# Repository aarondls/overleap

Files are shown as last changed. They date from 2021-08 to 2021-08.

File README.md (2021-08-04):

# Overleap

<p align="center">
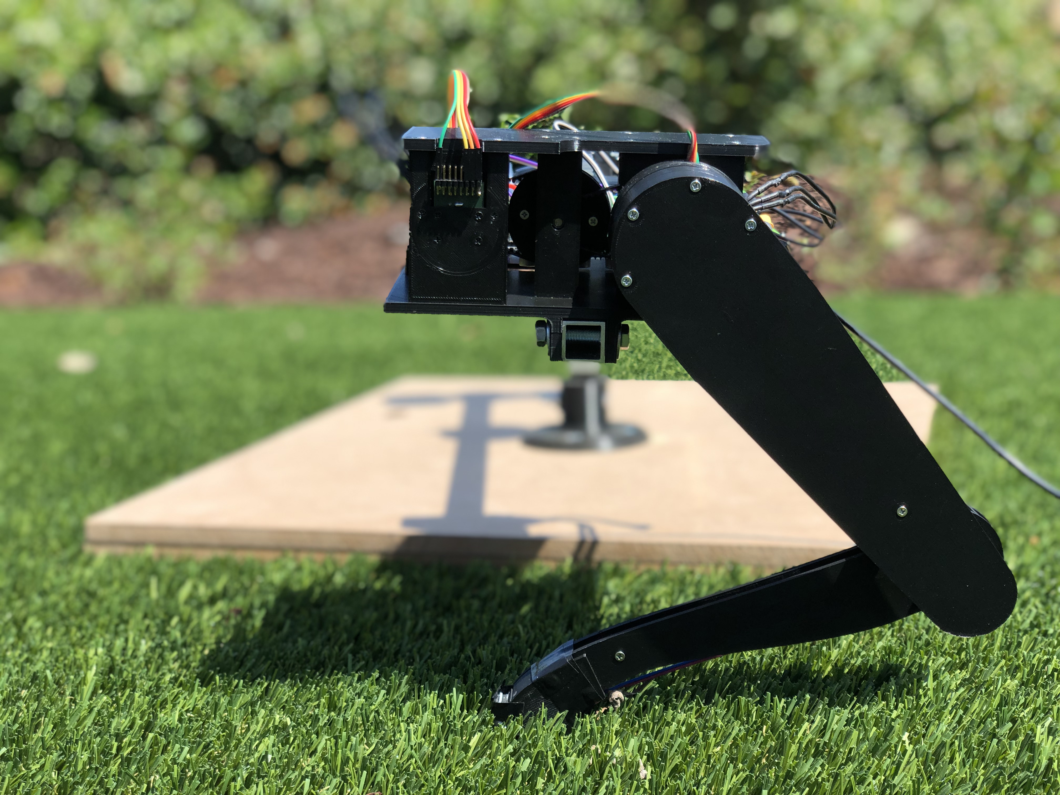
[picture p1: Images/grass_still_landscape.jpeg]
  
</p>

## Overview

Overleap is an open-source low-cost 3D printed dynamic robotic leg designed be as accessible as possible. Overleap can be assembled with a 3D printer and minimal tools, without CNC milling / waterjet cutting / laser cutting like other robotic legs. The building process is tailored to be simple and seamless, from the assembly manual to the programming method, creating a unique assembly experience.

Overleap is capable of executing quick and dynamic movements such as jumping and continuous hopping in a circle. This is made possible through Overleap's quasi-direct drive actuators and custom foot contact sensor. Jumping is controlled by directly manipulating joint torque, as calculated by the desired foot force and the Jacobian of the leg.

In the future, overleap is planned to be used in other legged projects, such as a low-cost quadruped robot.

## Capabilities

Overleap can perform a single jump

<p align="center">
  
</p>

as well as continous hopping in a circle

<p align="center">
  
</p>

The height and stance time of each jump, as well as horizontal speed of the leg, can be varied as desired.

## Design

<p align="center">
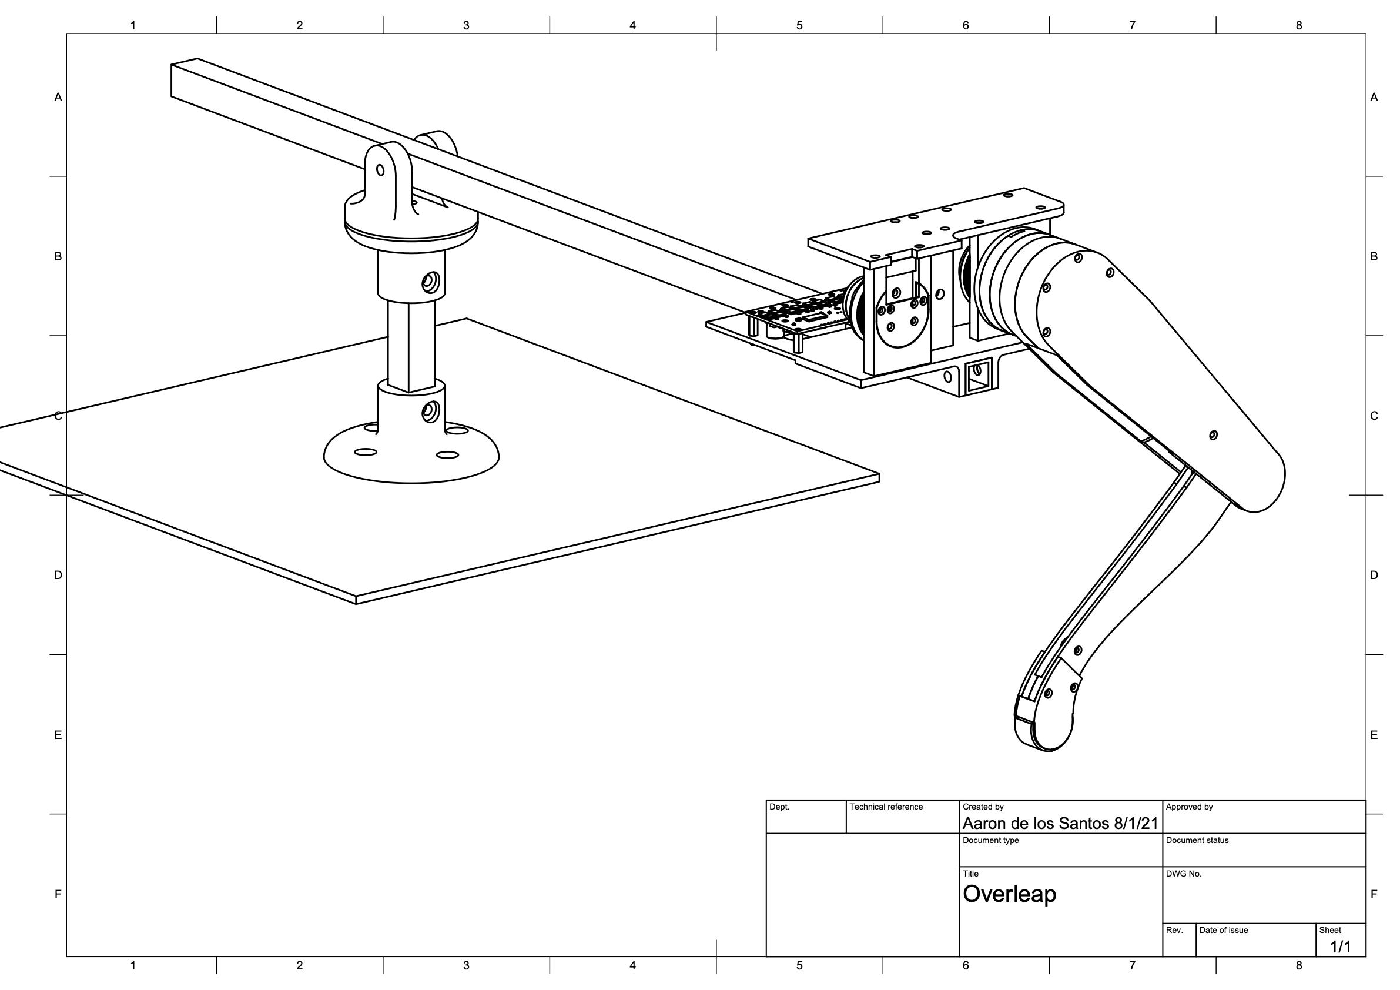
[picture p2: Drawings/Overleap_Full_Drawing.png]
  
</p>

### Quasi-Direct Drive Actuation

Overleap uses quasi-direct drive actuators to drive the leg. The motors are geared down 9:1, allowing for increased torque while having high backdrivability and bandwidth.

To keep the footprint small, the gear system for the hip joint is housed beside the hip, while the gear system for the knee joint is housed within the upper leg. The actuators are coaxial in the sense that the knee motor is on the same axis as the hip motor output shaft.

### Custom foot contact sensor

A custom foot contact sensor was developed to detect when overleap was on the ground. This foot sensor is cheap and requires no machining/moulding.

The foot sensor consists of a 3D printed frame and rubber outer padding for grip. Force detection is made possible through the use of a force sensitive resistor mounted between the outer foot pad and the frame.

The minimum actuation force of the foot sensor is around 10 grams, and can be increased in software depending on the desired conditions.

### 2 DOF rotating base

For testing overleap, the leg is attached to a rotating base with 2 degrees of freedom. This allows the leg to move in both the vertical and horizontal (circular) direction.

The base plate is made out of presswood, while the actual rotating mechanism consists of 3D printed parts. Square aluminum tubes are used as the stand and boom to attach the leg.

### Controlling leg movement

Overleap works by directly controlling the torque of both motors. The microcontroller sends ASCII commands through UART to the ODrive motor controller for the desired torque of each axis. The calculation for these values of torque depends on the current phase of the leg.

During the stance phase (when the foot is touching the ground), overleap calculates a sinusoidal force profile that provides the desired impulse to the leg, then applies this force profile throughout the duration of the stance phase. To calculate the necessary torque values that achieve the desired force at the foot, the transpose of the Jacobian is used.

During the aerial phase, overleap runs a PD control loop to hold a predefined position until the foot comes into contact with the ground. While inverse kinematics can be used to calculate the angles of the leg to achieve the desired foot position, overleap defines the foot position using the joint angles directly as it is easy to visualize where the foot would be.

### Force profile

The force profile in the vertical (y) direction is a sinusoidal curve, specifically of the form a sin^2(b pi t).  The parameters a and b are calculated based on the desired force impulse and stance duration, and t is the time (duration) of the force application. This allows for the regulation of jumping height as well as gradual application of force.

In the horizontal (x) direction, the force applied is a set proportion of the vertical force. Horizontal speed can then be modulated by defining the maximum horizontal force to be applied. On top of allowing for gradual force application, this also keeps the foot firmly in contact with the ground even on slippery surfaces by taking into consideration its coefficient of friction.

## Parts

The full parts list and STL models for the 3D printed parts are available at the [parts](Parts) folder.

## Assembly

### Mechanical assembly

Start by installing all the heat set inserts into the parts. After installing, they should sit flush against the plastic and feel secure when tightening screws into them.

Next, glue the magnets that came with the AS5047P encoder evaluation board onto the back of the motor. Super glue or epoxy can be used for this.

Line up the rubber pad against the inner sensing area of the force sensitive resistor and cut the rubber to the same size. This will be used as the foot pad later on.

At this point, we will need to jump ahead to one portion of the electrical assembly and solder the jumper wires to the encoder. Solder 5 cables to the A, B, I, 5V, and GND outputs of the encoder board. Take note which wire colors correspond to which outputs, as this will be needed later on.

Now, we can continue with the mechanical assembly. As they say, a picture is worth a thousand words, so this guide will be presented as a series of clean and simple drawings similar to Ikea manuals.

These illustrations are designed to be simplistic and intuitive such that the placement of screws, timing belts, and bearings can easily be inferred from them.

You can also view the [complete assembly guide](Drawings/Complete_Assembly.pdf) compiled as a single PDF.

<p align="center">
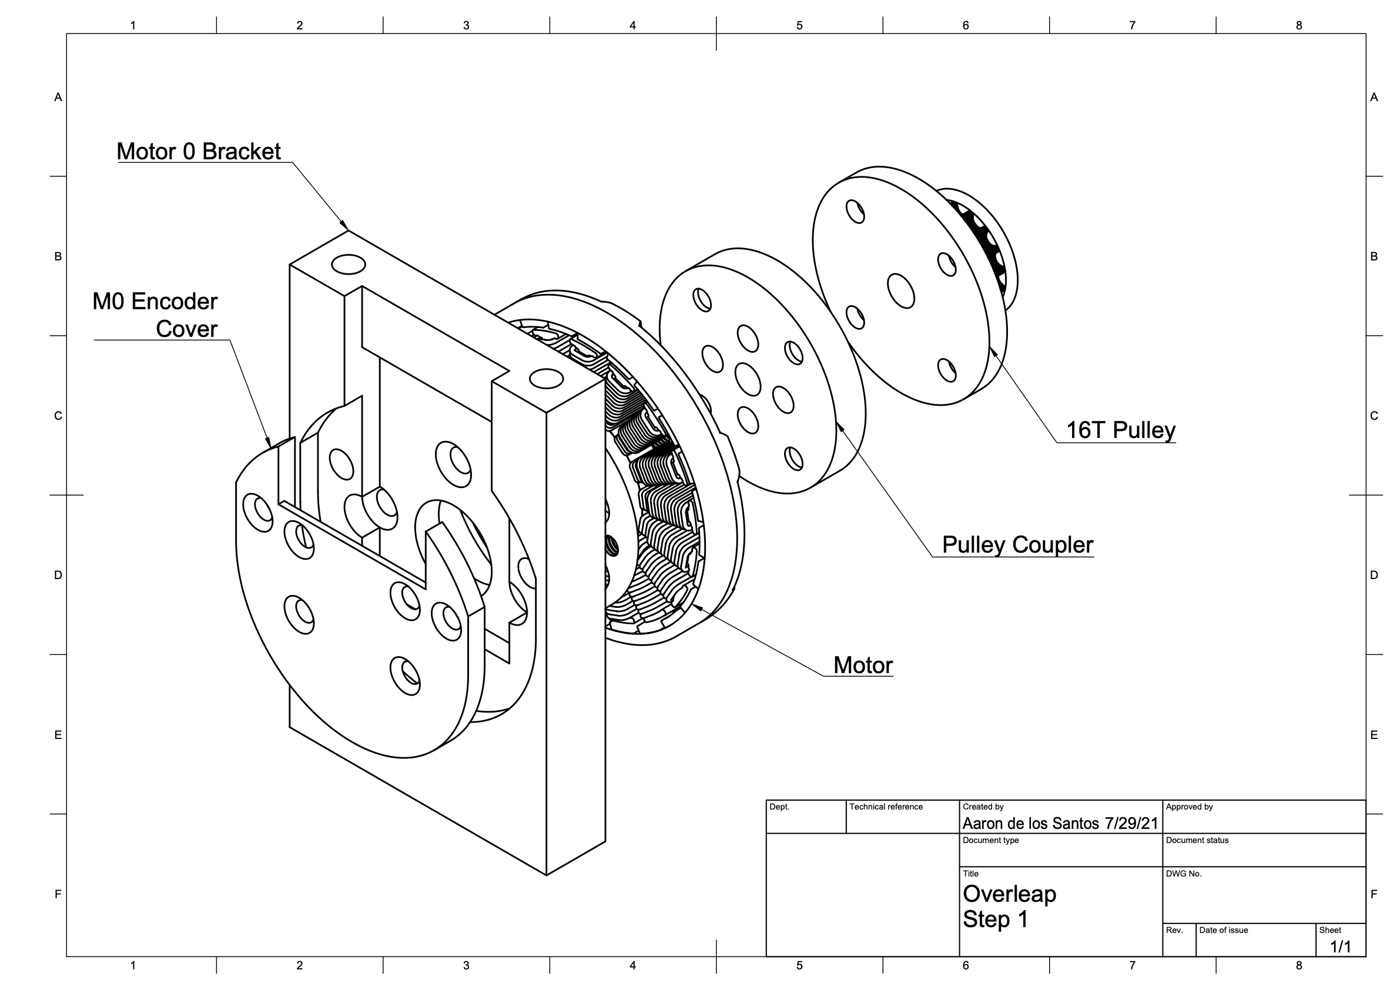
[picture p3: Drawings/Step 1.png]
  
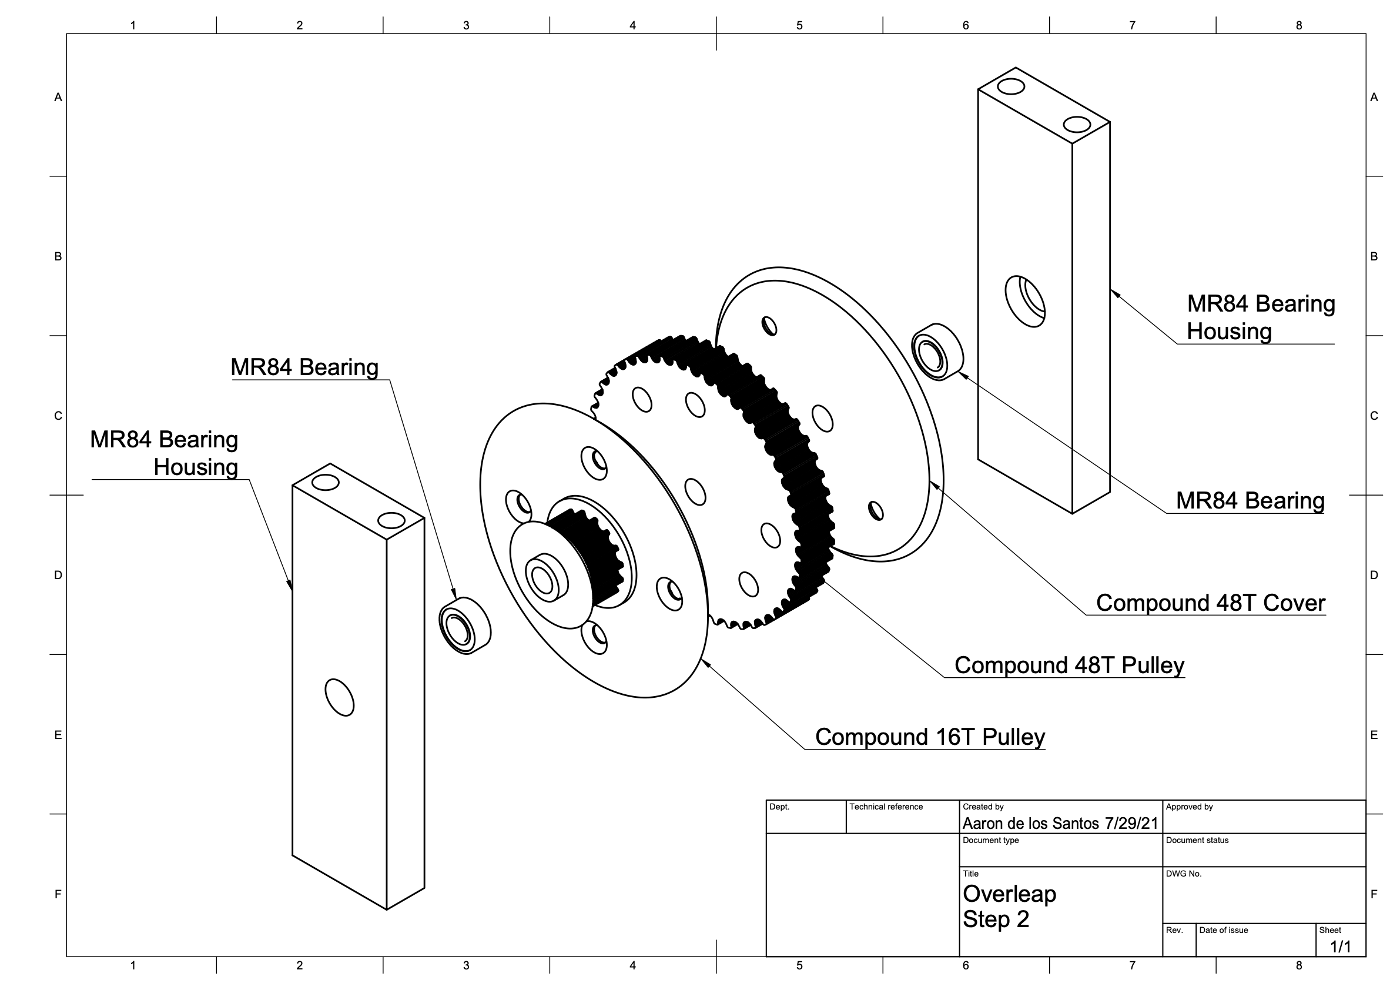
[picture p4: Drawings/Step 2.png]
  
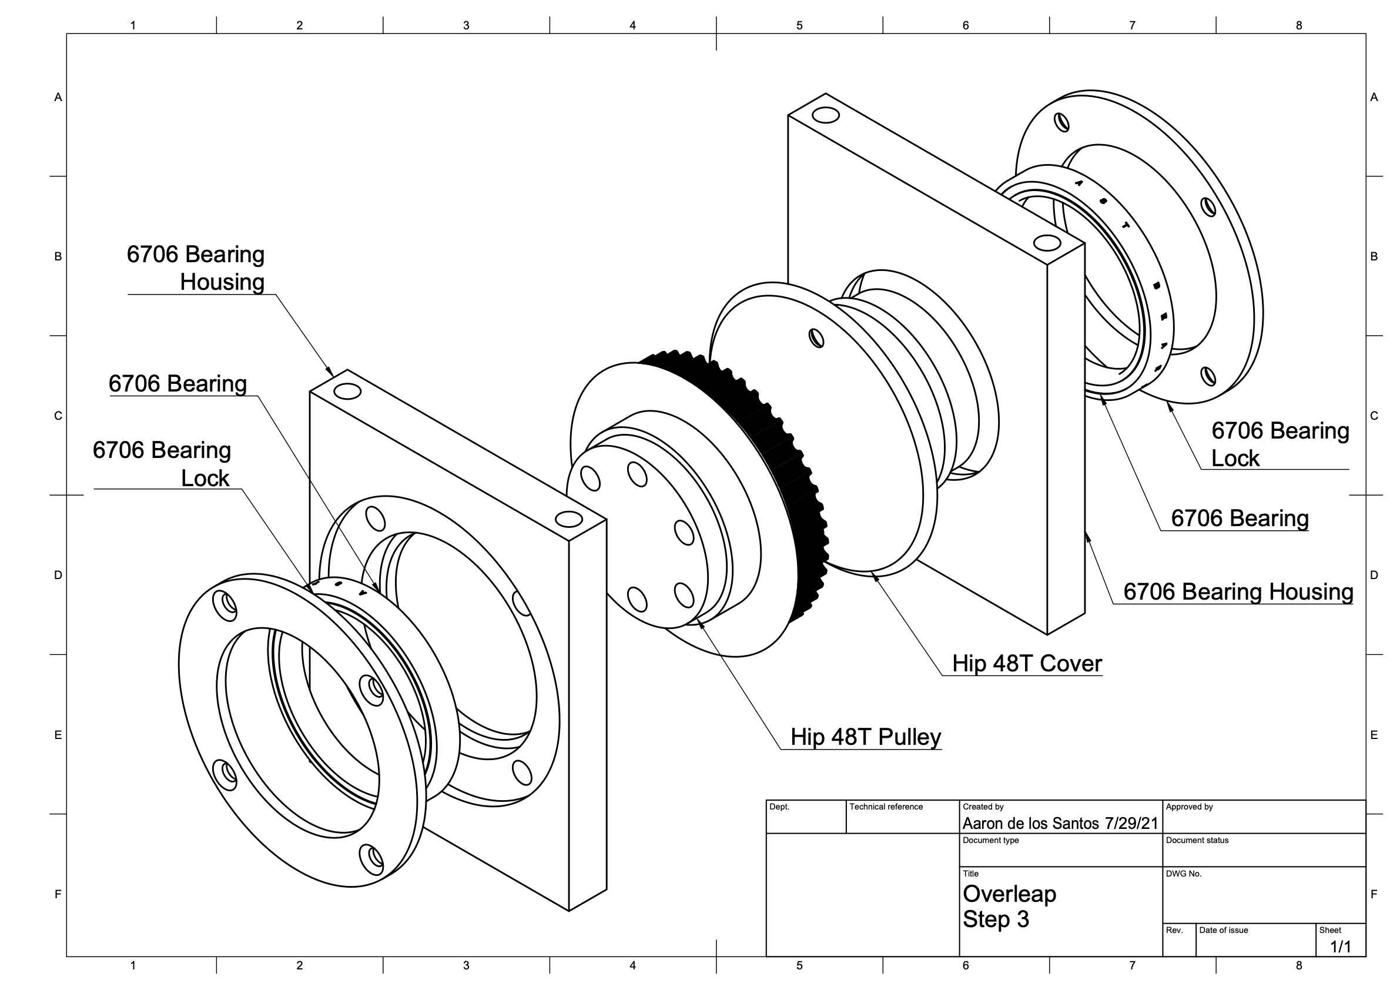
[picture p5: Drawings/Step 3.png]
  
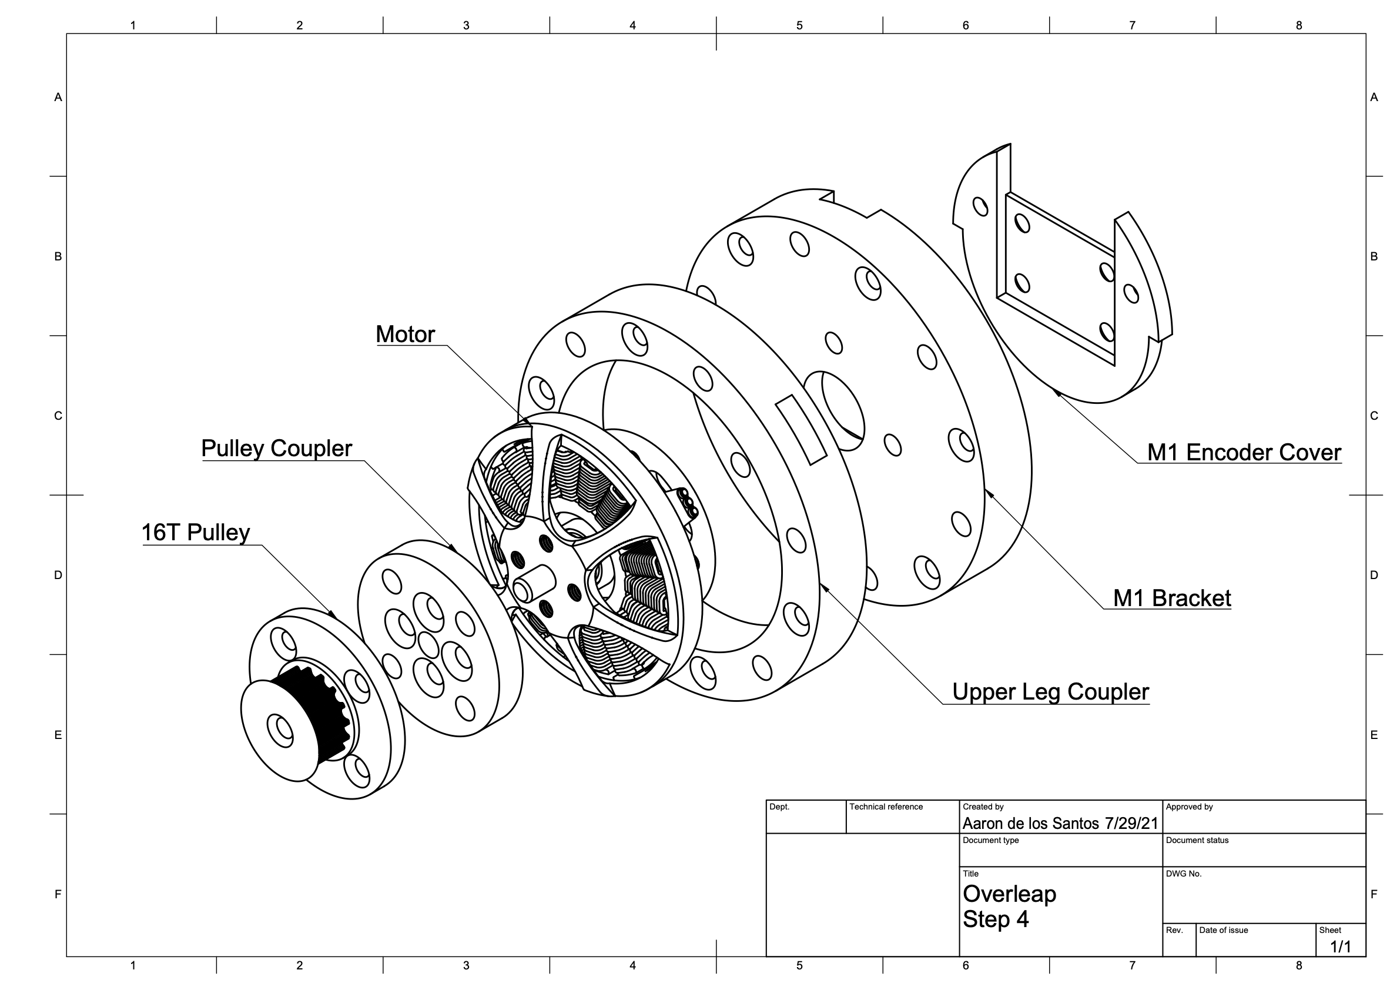
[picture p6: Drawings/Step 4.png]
  
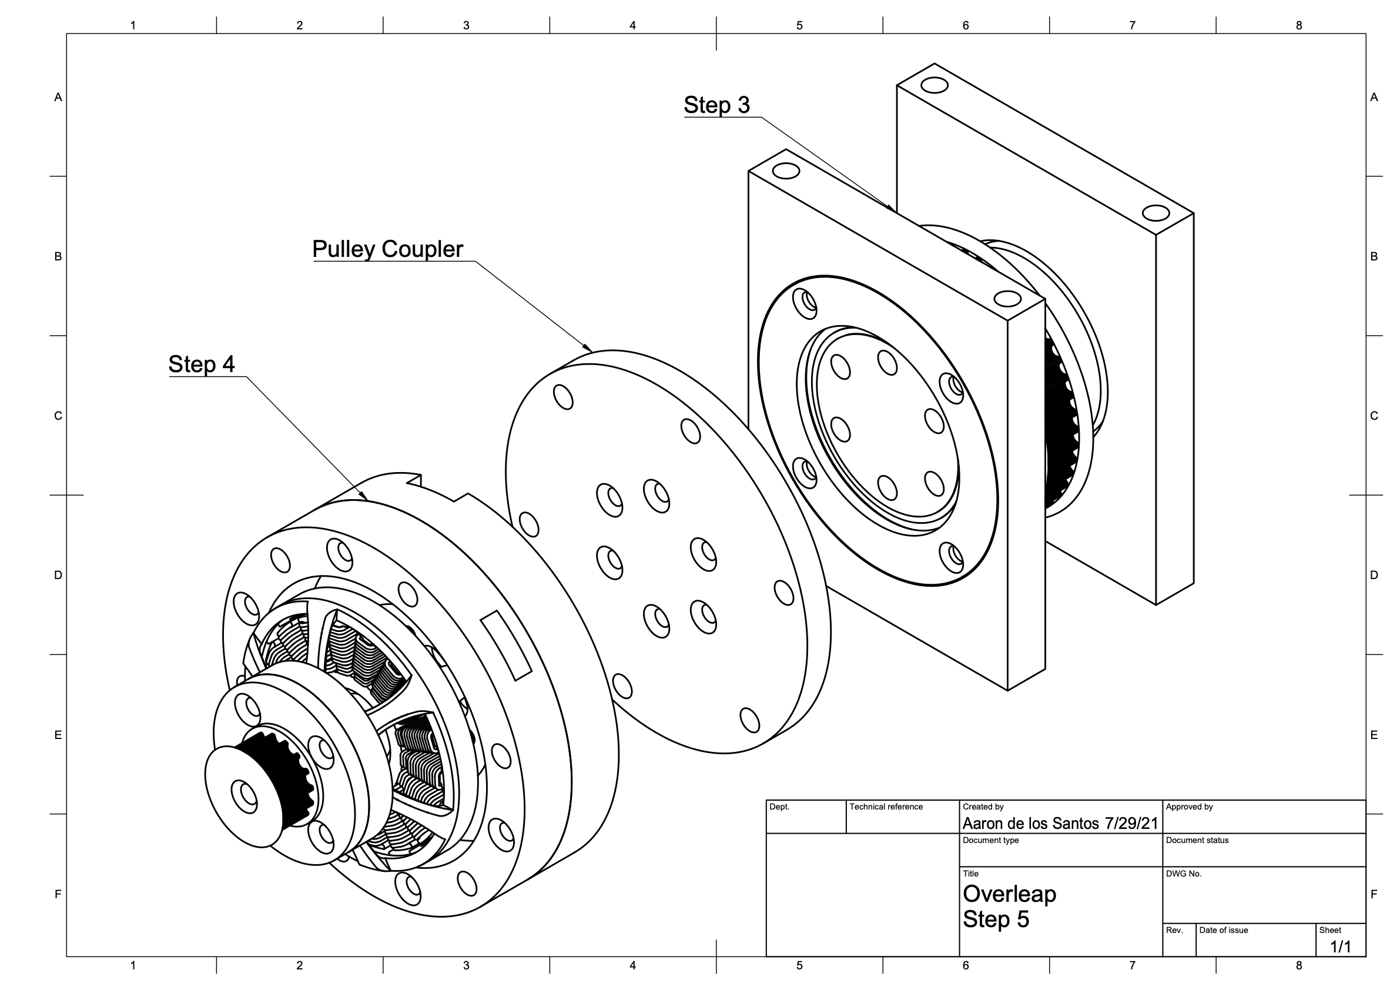
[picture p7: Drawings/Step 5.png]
  
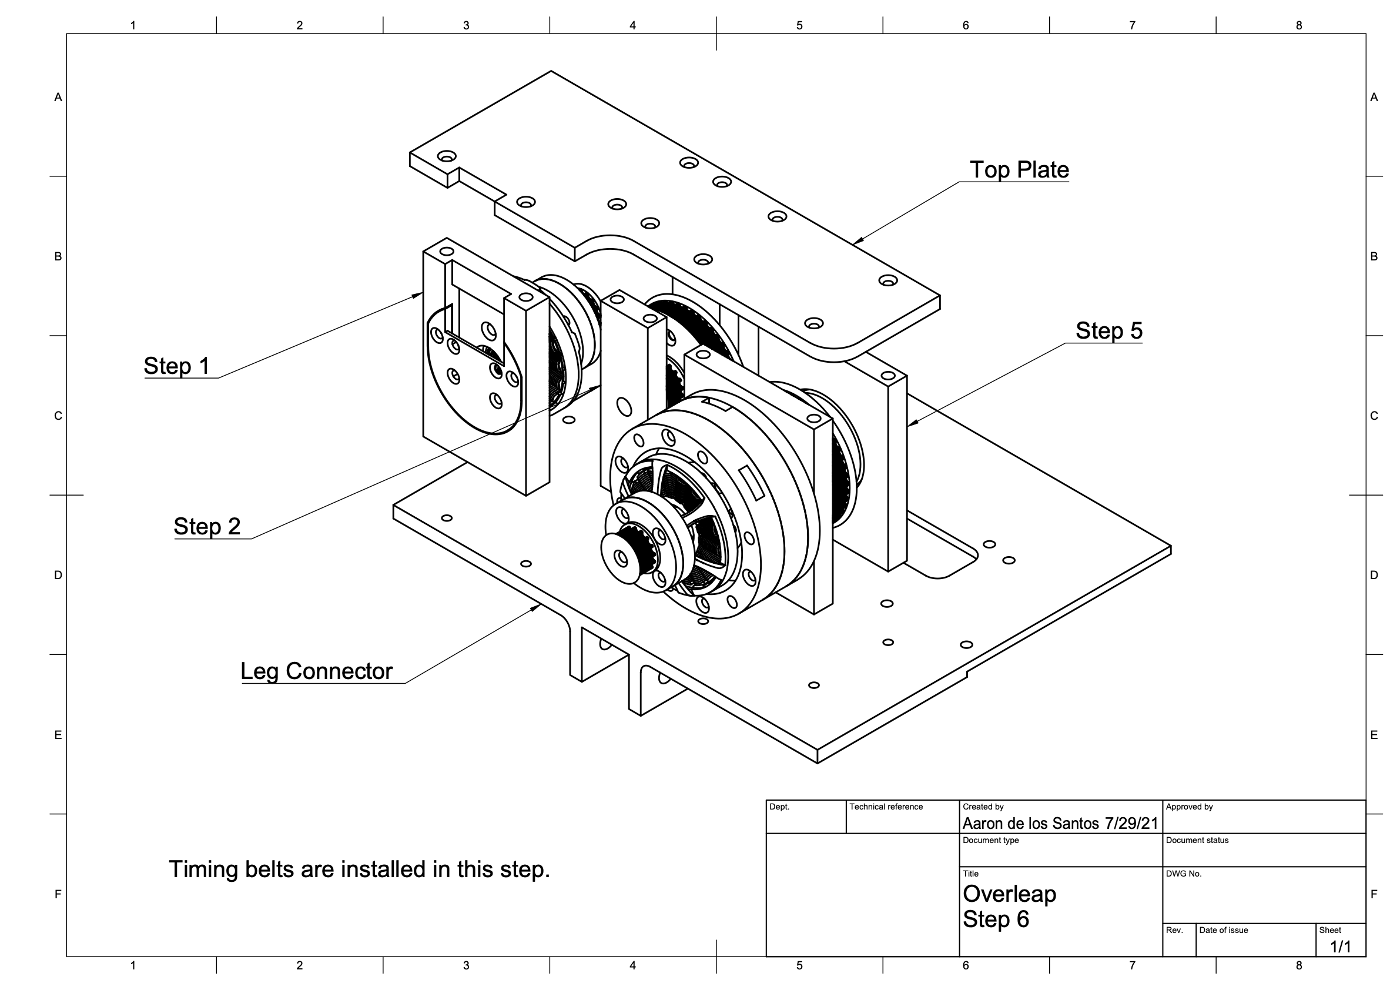
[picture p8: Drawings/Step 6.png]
  
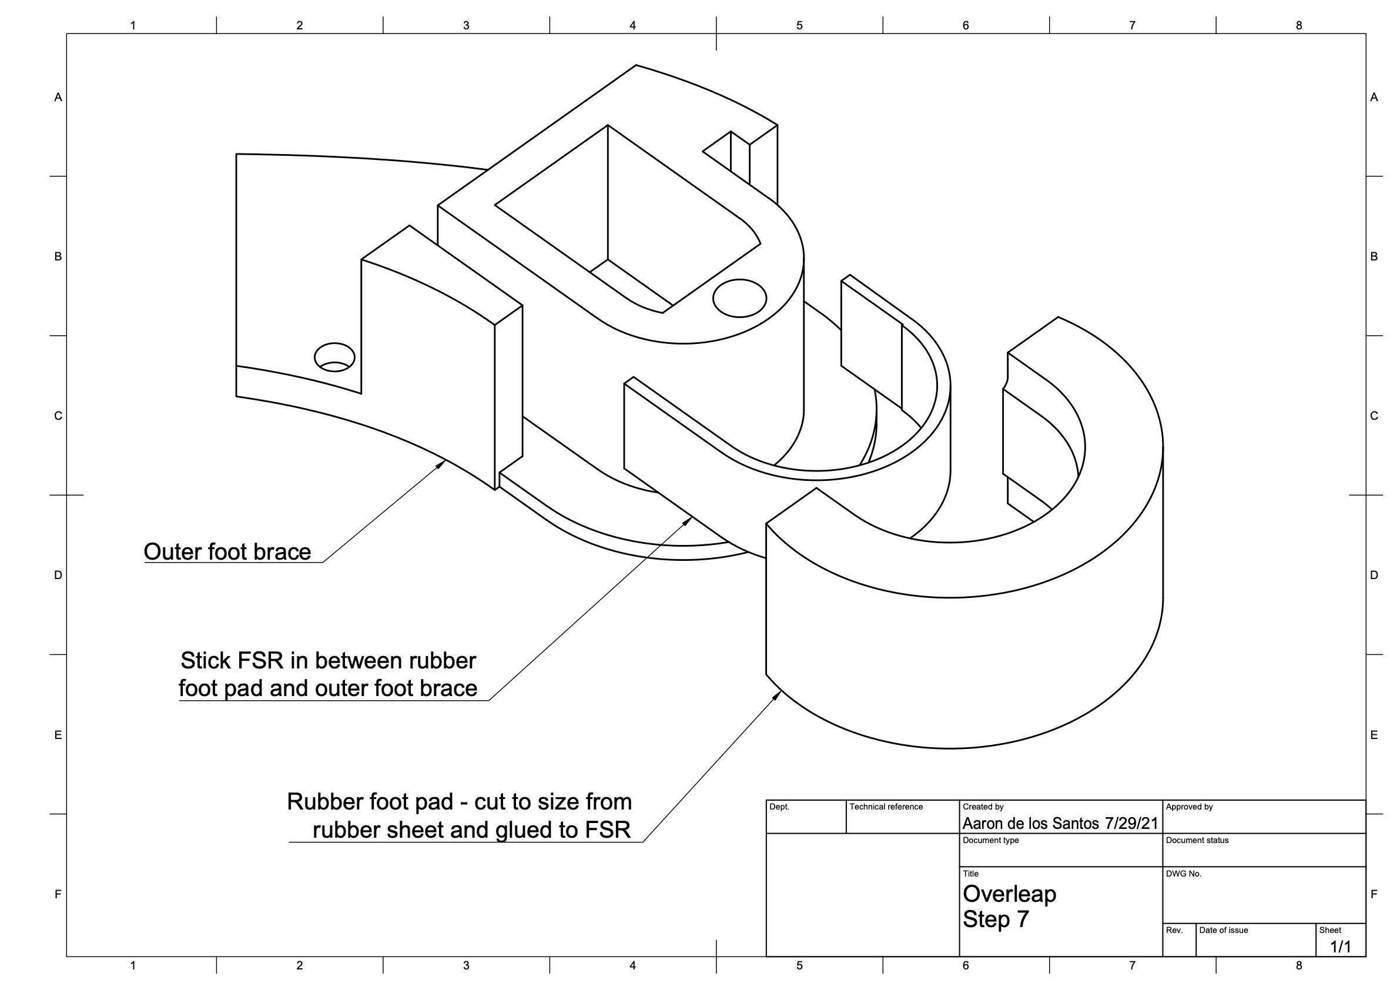
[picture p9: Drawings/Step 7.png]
  
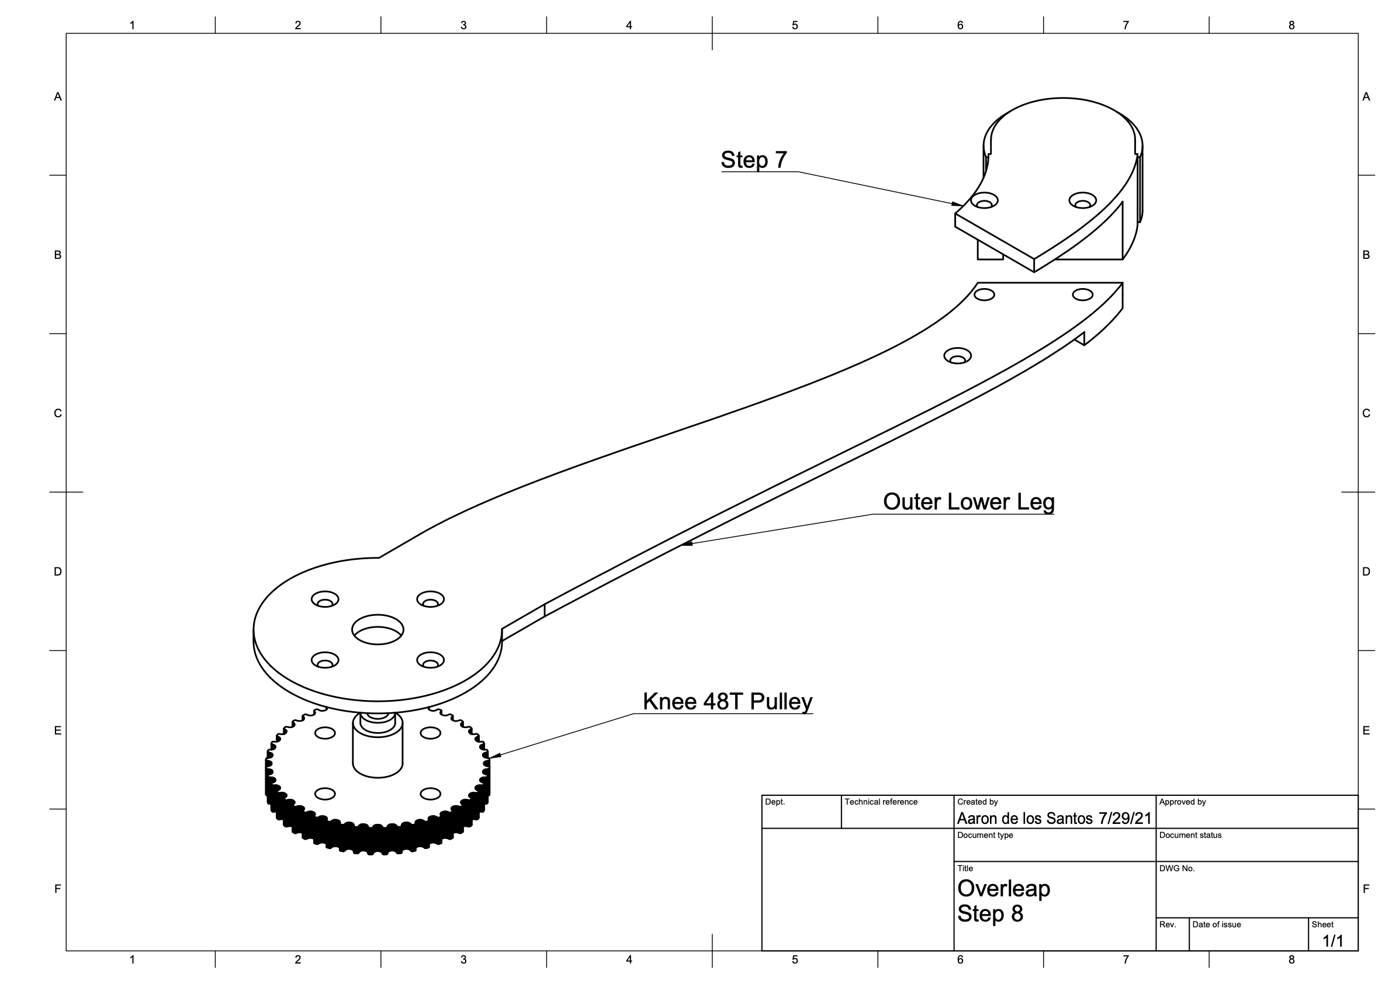
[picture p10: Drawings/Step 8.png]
  
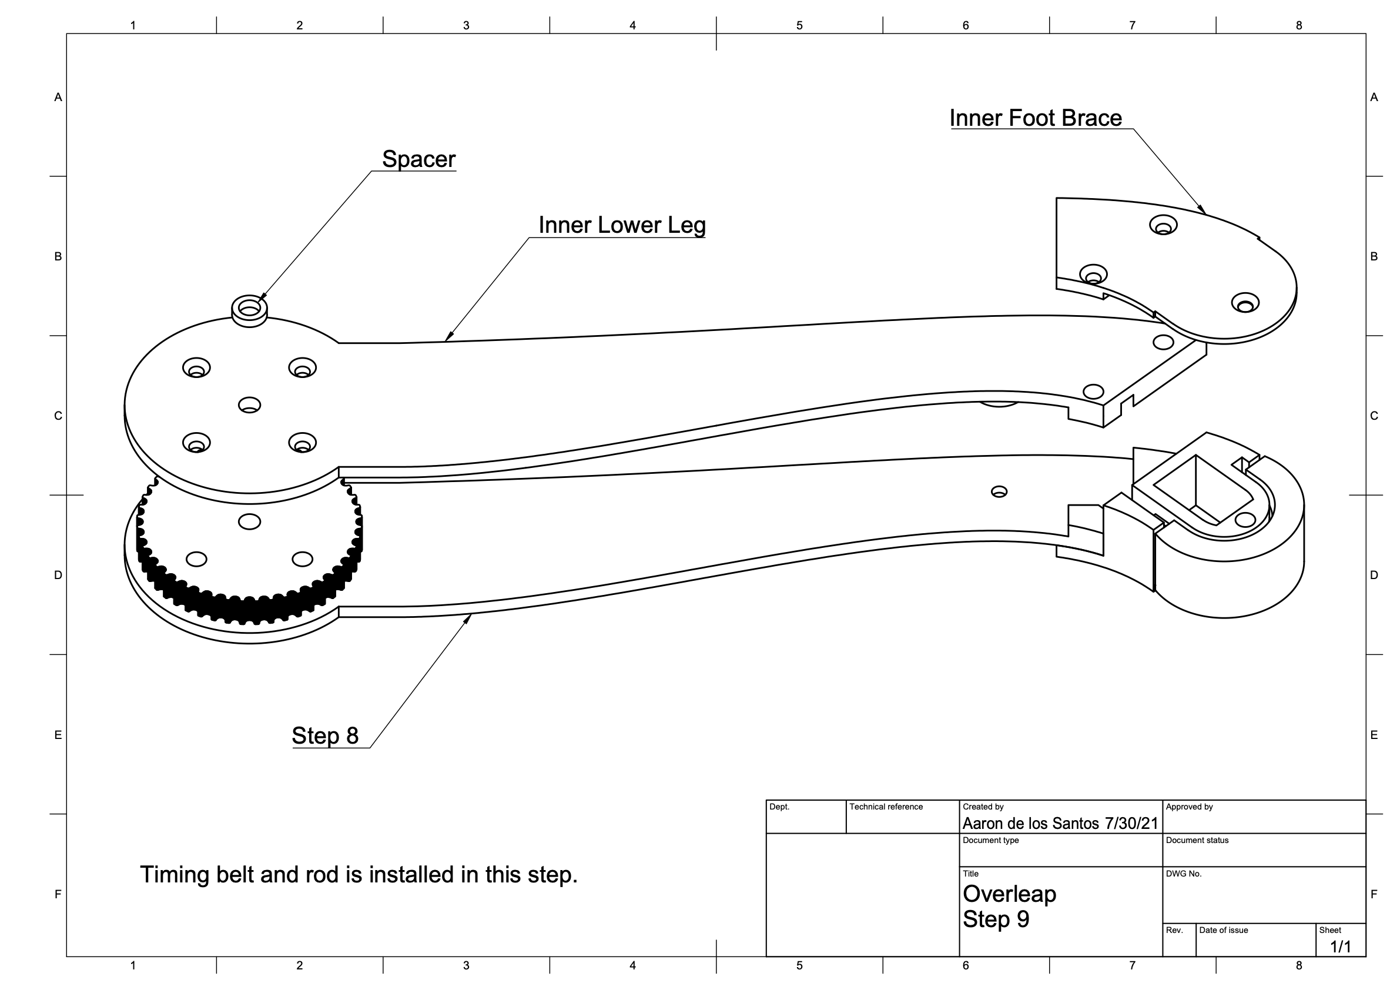
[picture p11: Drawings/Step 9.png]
  
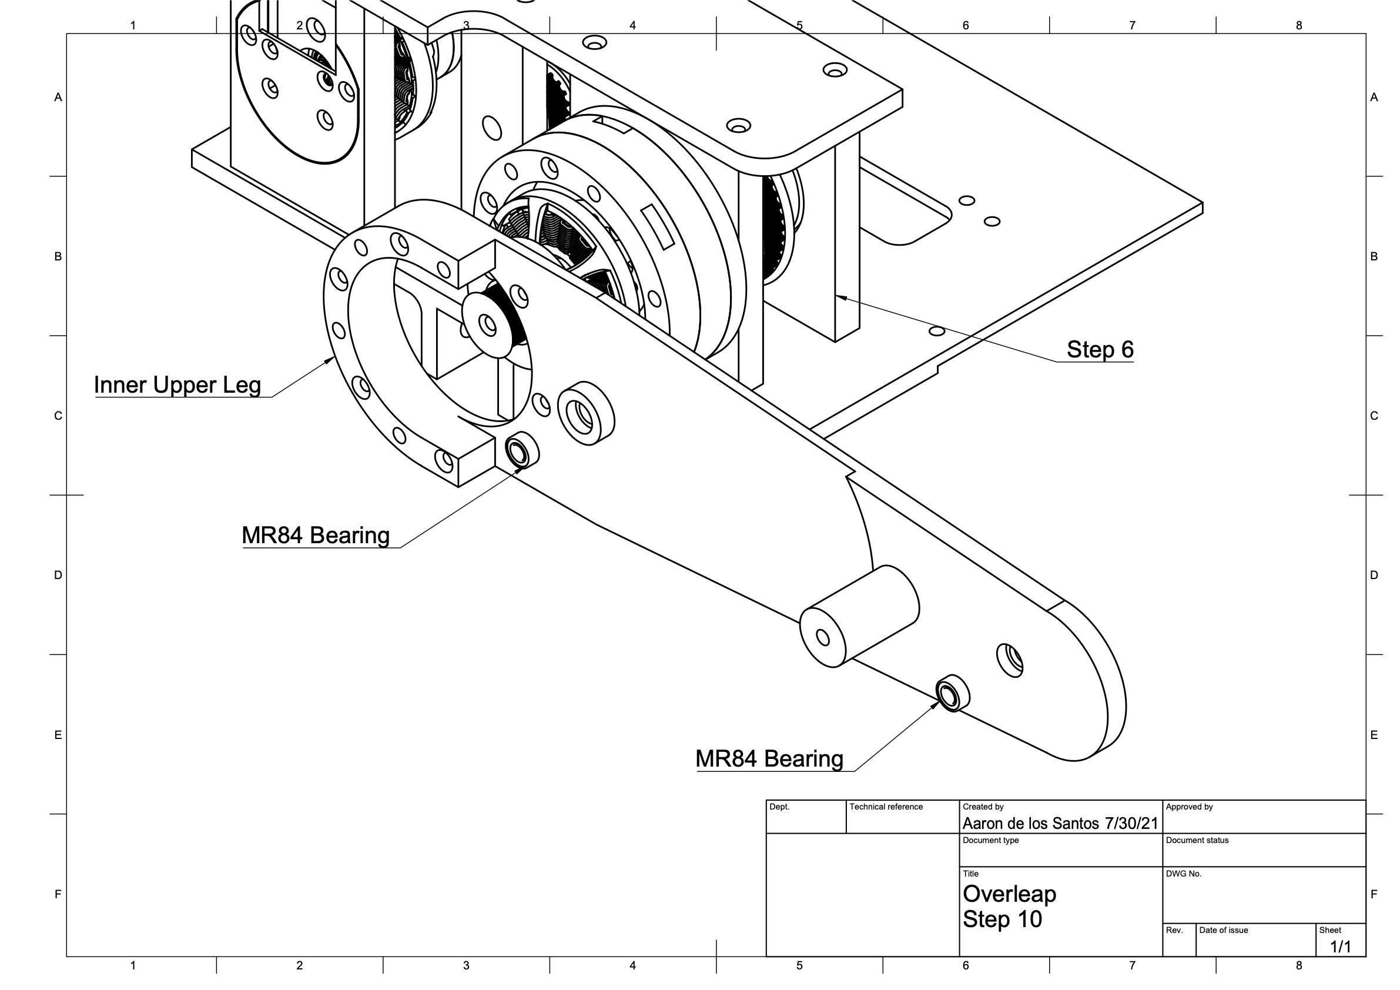
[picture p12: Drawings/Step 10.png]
  
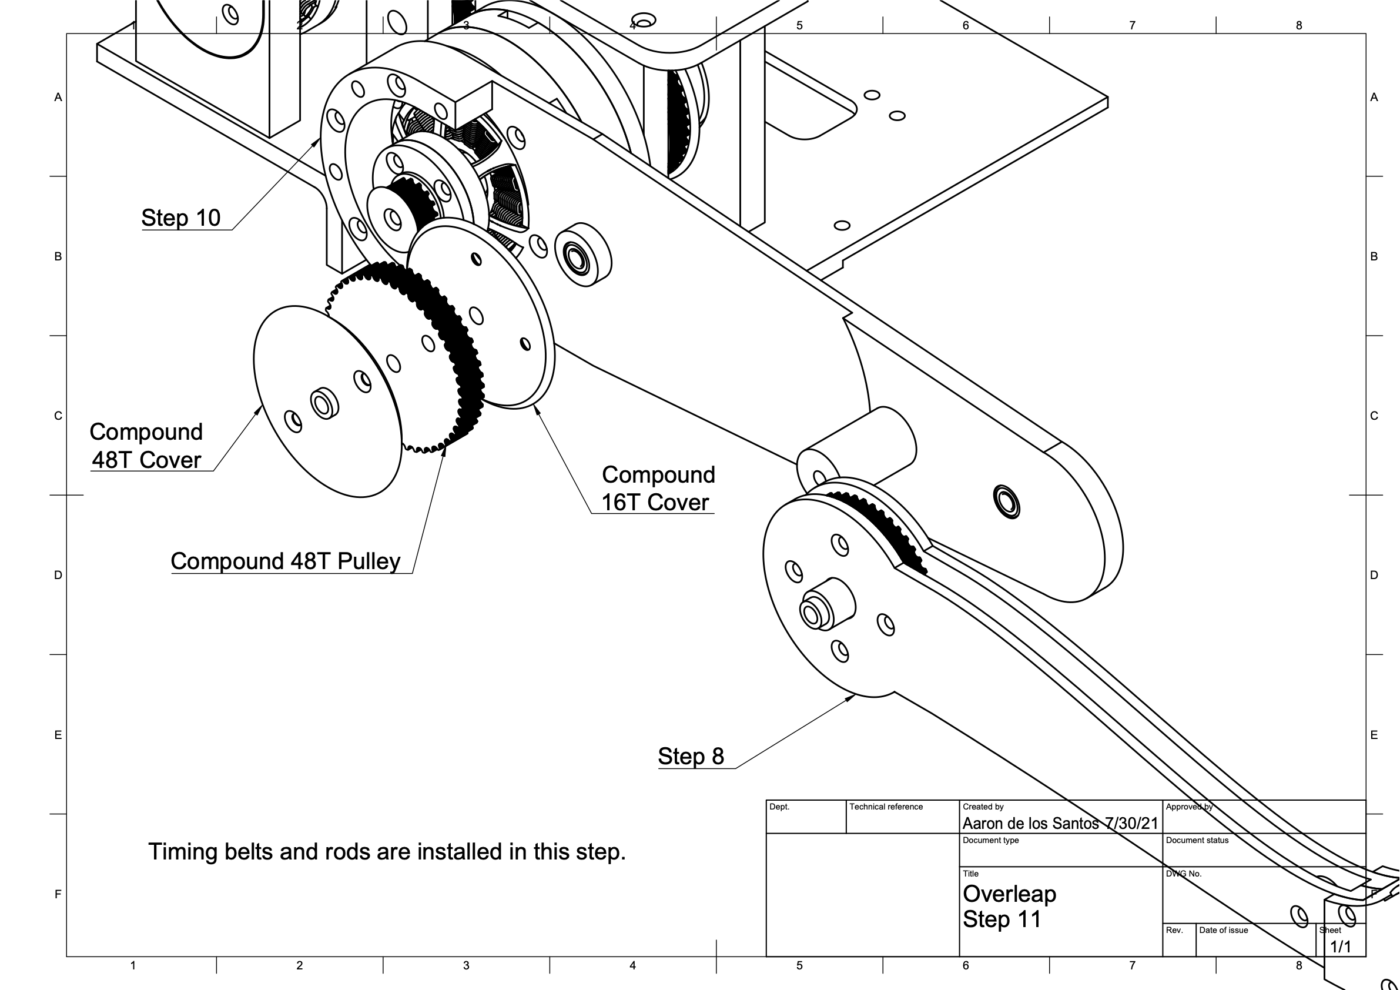
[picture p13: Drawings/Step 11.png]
  
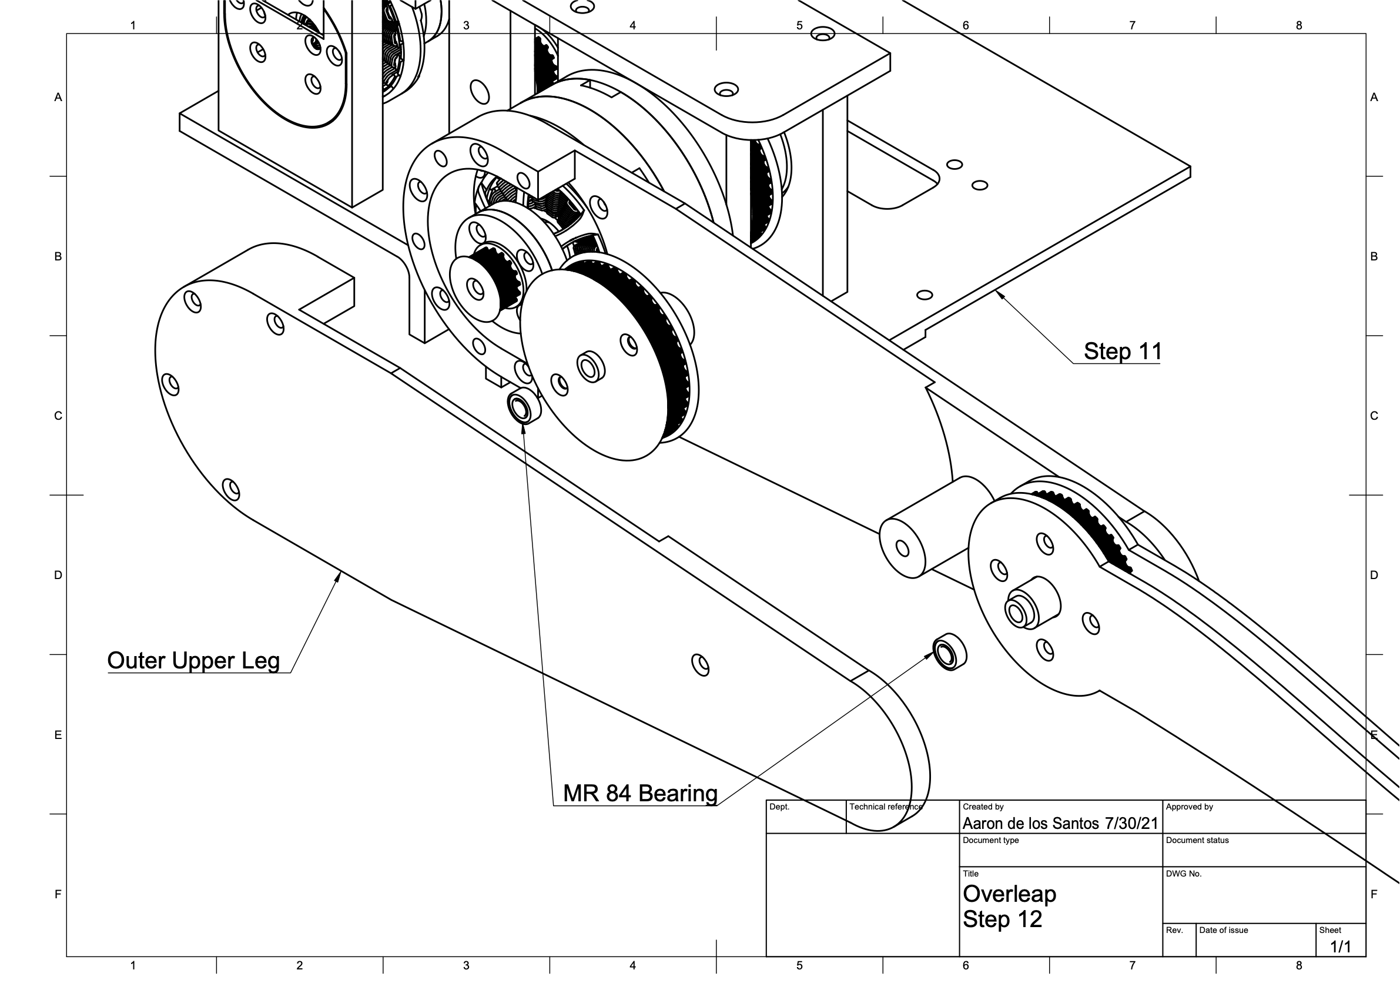
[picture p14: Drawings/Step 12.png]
  
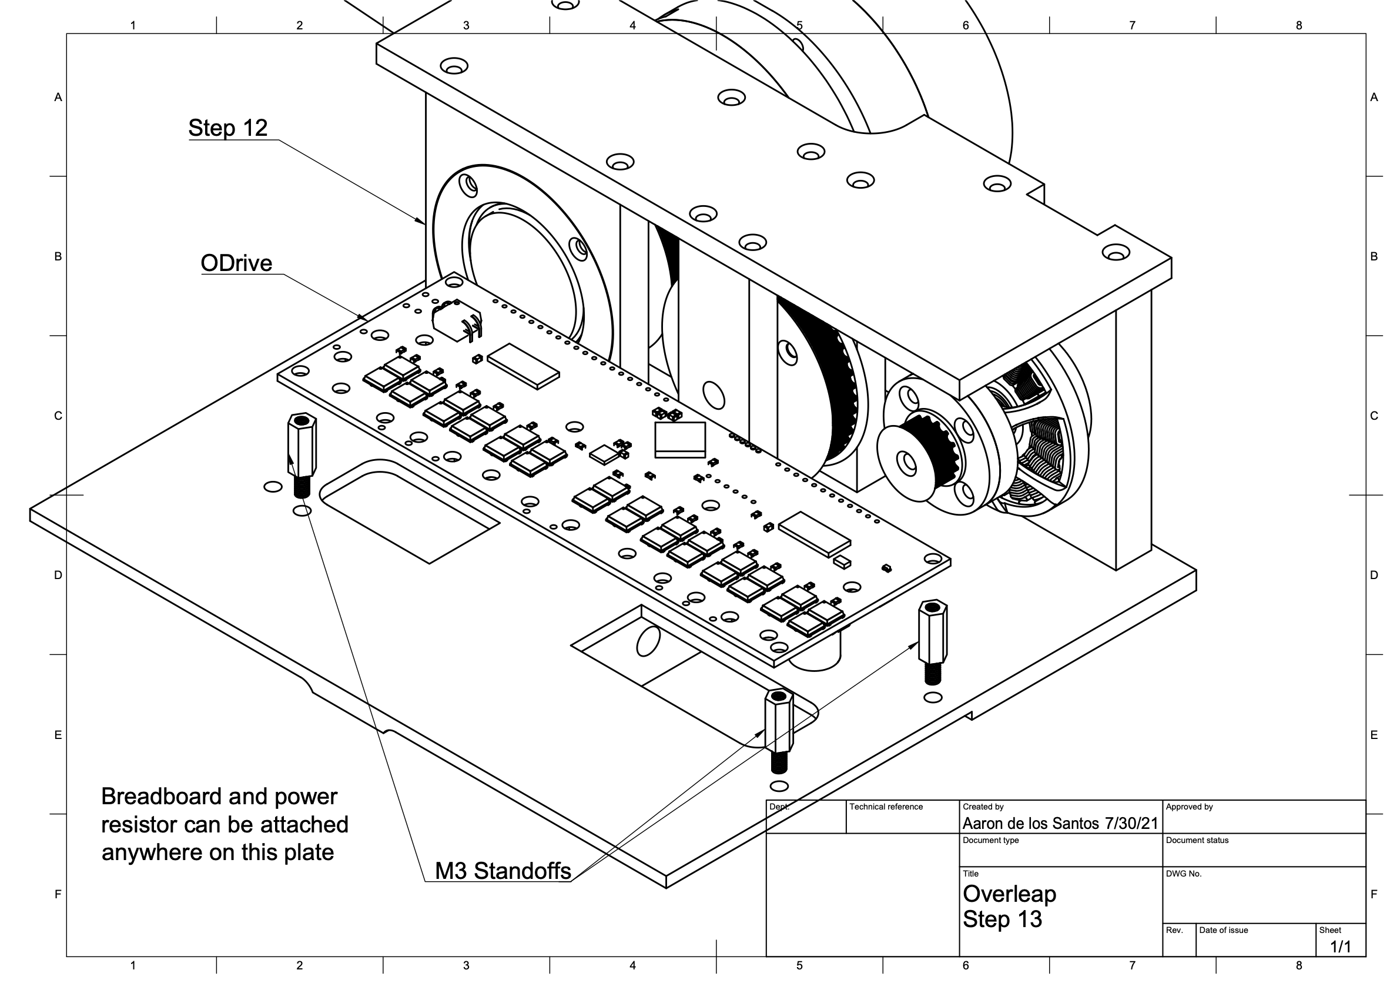
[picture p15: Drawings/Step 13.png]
  
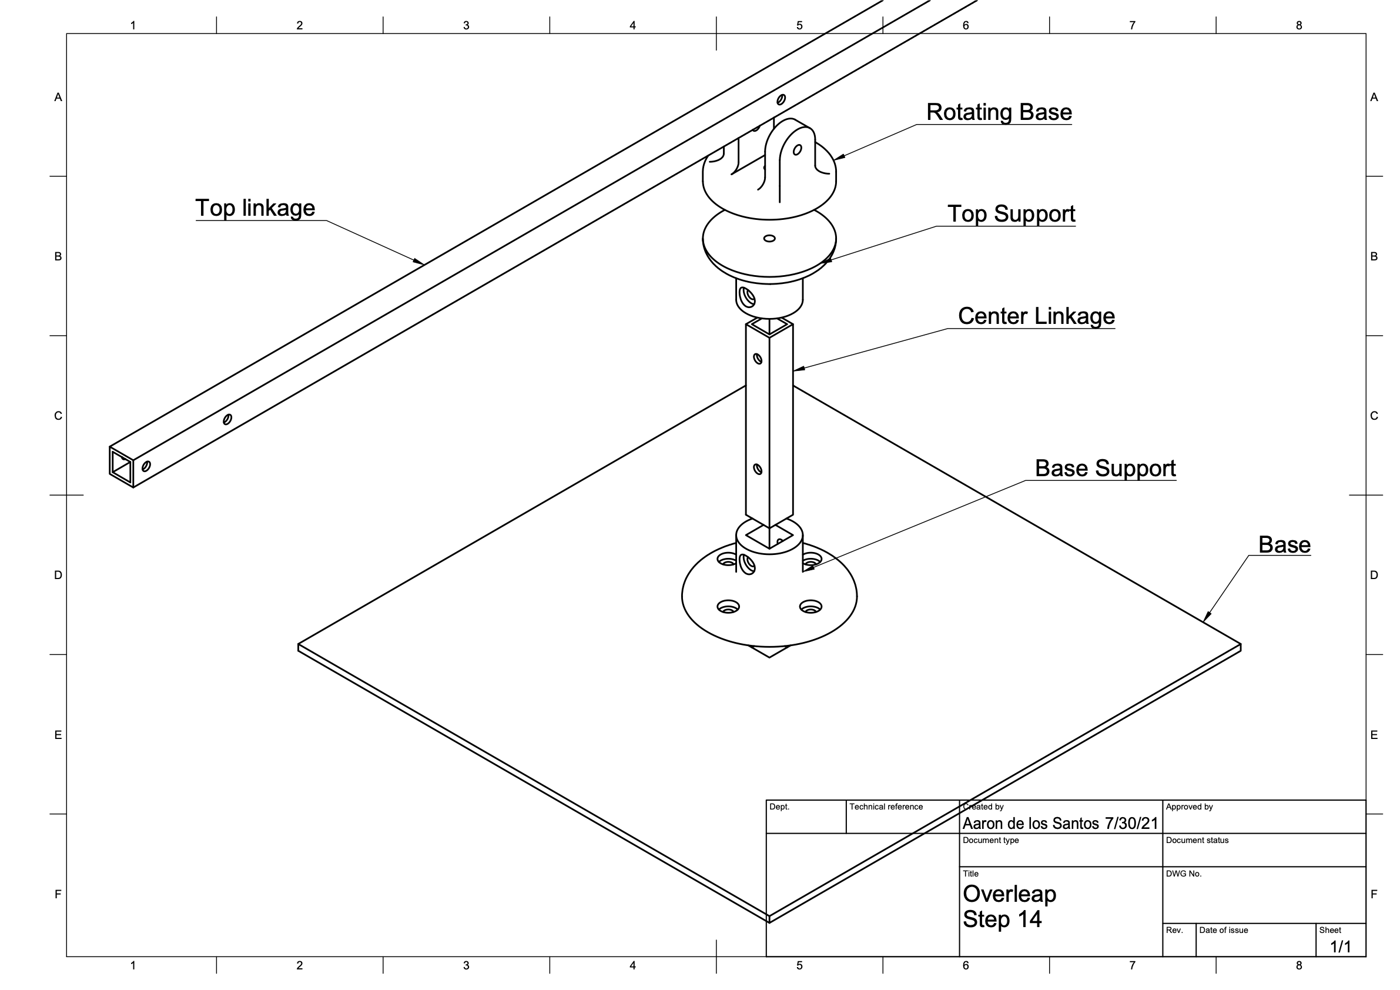
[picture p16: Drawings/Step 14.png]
  
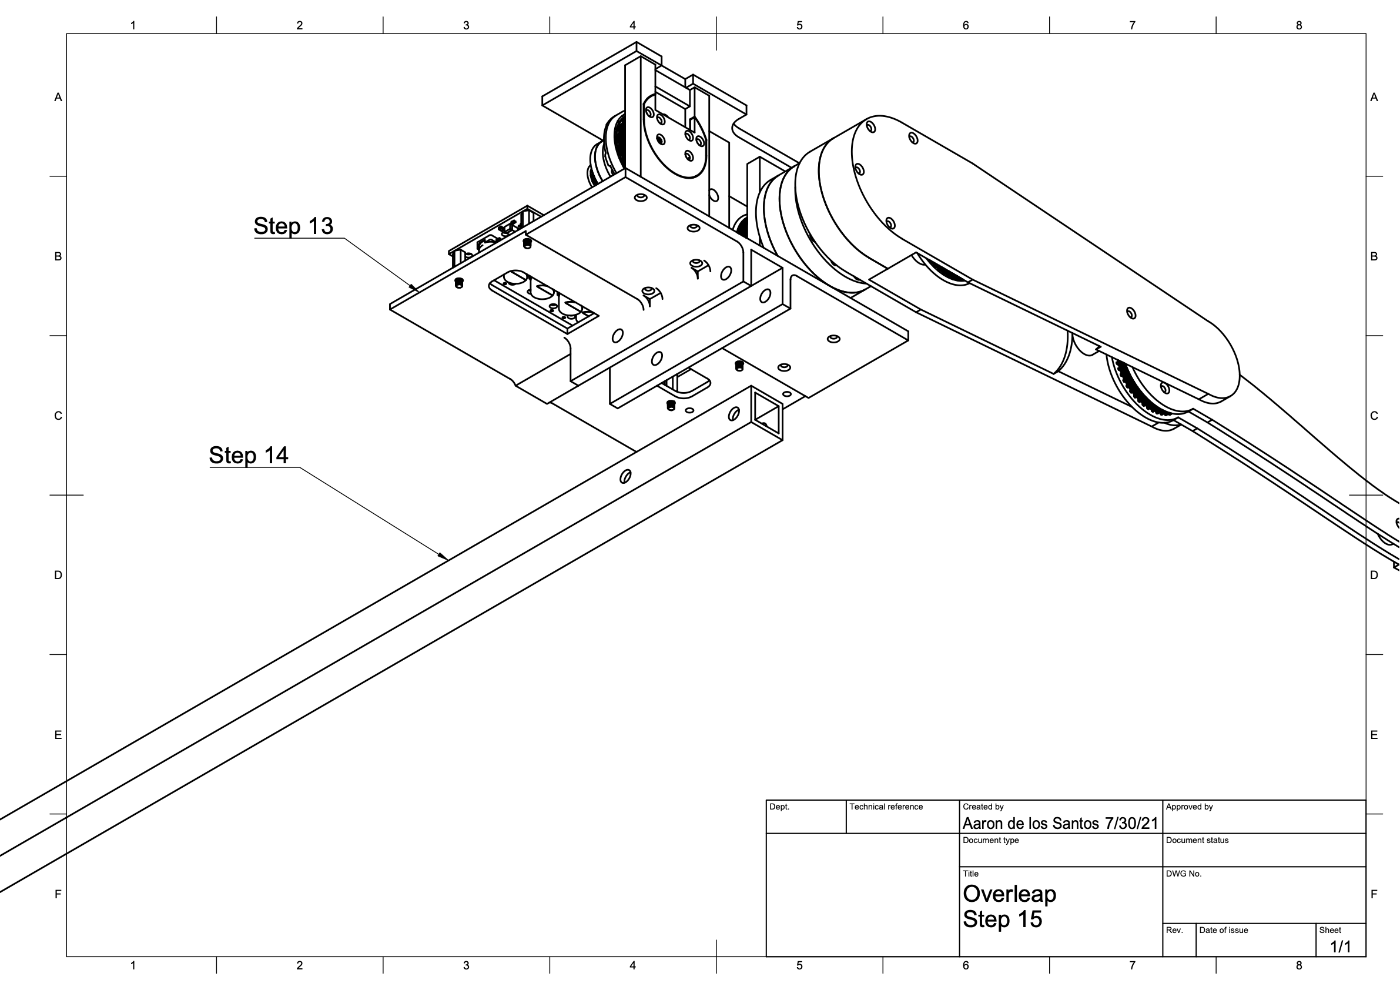
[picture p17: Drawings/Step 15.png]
  
</p>

### Electrical assembly

The electronic schematic for overleap is as follows:

<p align="center">
  
</p>

A power resistor can also be attached to the ODrive motor controller, if your power supply cannot dissipate excess current.

## Programming

### ODrive Set-up

As a side note, I wrote a [separate guide](https://github.com/aarondls/motor-position-control) on starting with the ODrive motor controller. This may be handy with getting familiar with ODrive.

Start by configuring the motors. Follow the "Configure M0" part on the ODrive [Getting Started](https://docs.odriverobotics.com/#configure-m0) page for both axis 0 and axis 1. The parameters used here are based on the T-Motor 4006 and AS5047 encoder:

* Current limit at 10A
* Velocity limit at 15 turns/sec
* Calibration current at 10A
* Pole pairs (number of magnet poles divided by 2) at 24 magnets / 2 = 12
* Torque constant at 8.27 / 380KV = 0.02176315789
* AS5047 CPR at 4000

Overleap will also use these additional configurations:

```bash
odrv0.config.enable_brake_resistor = True
odrv0.config.brake_resistance = 0.5
odrv0.config.dc_max_negative_current = -0.1
odrv0.config.max_regen_current = 0.5
```

Save the configuration and reboot.

```bash
<odrv>.save_configuration()
<odrv>.reboot();
```

Next is the motor calibration. Refer to the [AxisState](https://docs.odriverobotics.com/api/odrive.axis.axisstate) page for more information.

Begin by setting `motor.config.pre_calibrated` to `False`:

```bash
<odrv>.<axis>.motor.config.pre_calibrated  = False
```

Then, calibrate the motor:

```bash
<odrv>.<axis>.requested_state = AXIS_STATE_MOTOR_CALIBRATION
```

This just makes a beeping noise without moving the motor.

Now, set `motor.config.pre_calibrated` to `True`:

```bash
<odrv>.<axis>.motor.config.pre_calibrated = True
```

Save the configuration and reboot. Repeat this for both axis.

Finally, calibrate the encoders. For Overleap, ODrive interfaces with the AS5047 encoder through ABI. Follow the [Encoder with index signal](https://docs.odriverobotics.com/encoders.html#encoder-with-index-signal) part for both axis.

ODrive will search for the encoder index manually, so set `startup_encoder_index_search` to `False`.

```bash
<axis>.config.startup_encoder_index_search = False
```

This means that at every boot-up, Overleap will call

```bash
<axis>.requested_state = AXIS_STATE_ENCODER_INDEX_SEARCH
```

for each axis.

Note if motor wires are switched, make sure to run through this full calibration sequence again.

### Overleap Arduino library installation

The Overleap Arduino library is located at the [Overleap folder](Overleap). To install, follow these steps.

1. Download the Overleap folder. This may require cloning the repository.

2. In the Arduino IDE, select Sketch -> Include Library -> Add .ZIP Library.

3. Select the enclosing Overleap folder and hit Choose. Restart the Arduino IDE.

4. Verify that the Overleap library was installed by navigating to File -> Examples, and checking for the OverleapExample sketch.

This library provides an easy-to-use interface for Overleap that we will examine through the example sketch.

### Example sketch

The OverleapExample sketch has everything needed to get started with Overleap. It contains all the necessary code for the prechecks and demonstrates how to program Overleap.

For the remainder of the programming guide below, we will be using this example sketch.

### Prechecks

Before starting, we will need to run through a few checks to ensure everything functions as we expect. Start by ensuring the ODrive motor controller is properly set-up. Next, upload the OverleapExample sketch to the microcontroller.

Overleap will begin searching for the encoder index signal, starting with motor 0, then motor 1. Make sure that the leg has ample room to move around during this phase.

After searching for the encoder index, the list of available commands is printed out to the serial monitor. The ODrive vbus voltage is also printed out, and warns if voltage falls below 12V.

Since we are interfacing with the AS5047 encoder through ABI, we will need to calibrate where the zero degree position for the leg is. This zero degree position is where both θ<sub>0</sub> and θ<sub>1</sub> is zero degrees, where θ<sub>0</sub> is the angle of the upper leg with respect to the horizontal and θ<sub>1</sub> is the angle of the lower leg with respect to the upper leg. The angles θ<sub>0</sub> and θ<sub>1</sub> are illustrated by the diagram below.

<p align="center">
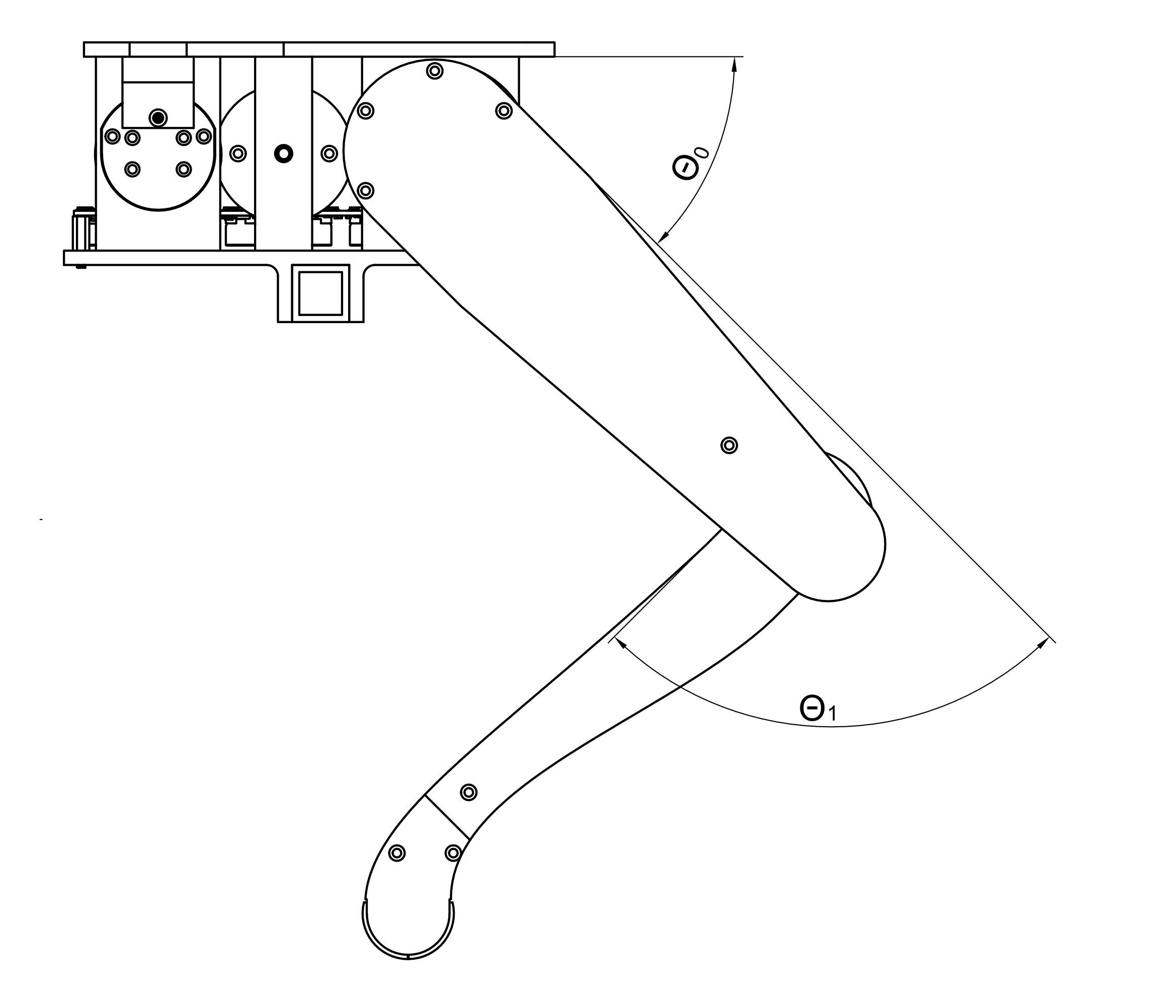
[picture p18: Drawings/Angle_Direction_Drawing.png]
  
</p>

Type the character 'c', then follow the ensuing instructions to calibrate the zero degree position. Once finished, you can view relevant information of the leg, such as position in degrees and velocity in degrees per second for both axis, by typing the character 'd'.

We will need to verify that for axis 0, commanding positive torque results in clockwise rotation, while for axis 1, positive torque results in counterclockwise rotation. The reason for axis 0 being inverted compared with the convention is that ODrive uses the encoder rotation for direction, so simply swapping two wire leads will not change motor direction.

For this step, hold the leg to avoid it moving towards extreme angles. Type the character 'y' to begin this check. Overleap starts by moving motor 0, then waits for your confirmation before moving motor 1. Take note which direction the axis moves. If the motor does not move in the direction we expect, verify that your encoder wiring is correct. A swapped A and B wire could result in opposite rotation.

At every start-up, this sequence remains the same, except for verifying positive torque direction. Overleap begins by searching for the encoder index signal on both axis. Then, calibration of the zero degree position is needed. Finally, it is a good idea to verify that Overleap reads the correct degree position of the leg.

### Single jump

To perform a single jump, type the character 'j'. Let us examine the code in-depth to see how this works.

Before starting the jump, we need to ensure the current phase is on `TOUCHDOWN_PHASE`, as we start on the ground. This is done by calling the `SetCurrentPhase` function with the desired phase as the argument.

```c++
leg.SetCurrentPhase(TOUCHDOWN_PHASE);
```

Now, we are ready to control the leg, so we call the `EnterTorqueControl` function.

```c++
if (!leg.EnterTorqueControl()) {
  Serial.println("Aborting.");
  return;
}
```

`EnterTorqueControl` returns false if it is unable to sucessfully enter torque and closed loop control on the ODrive, so we print the abort message and stop if anything goes wrong.

After this, we set the desired impulse of the jump with the `UpdateForceProfile` function, with the desired impulse, desired maximum fx force, and proportion of fy applied as fx as the arguments. Impulse is in units of Newton millisecond, while force is in Newtons.

```c++
leg.UpdateForceProfile(2500.0f, 0, 0.4f);
```

In this case, we set fx_max to 0 since we want a single jump to go straight up.

Now, everything is set-up for a jump. The next thing to do is put the leg into a good starting position for jumping using the `HoldPosition` function.

```c++
leg.HoldPosition(25.0f, 110.0f, false, 3000);
```

The first two arguments tells Overleap to hold the position with θ<sub>0</sub> of 25 degrees and θ<sub>1</sub> of 110 degrees. The third argument is an end_at_touchdown boolean that signals whether the position hold should end if touchdown is detected (if the foot hits the ground). The fourth argument is the maximum time of the position hold in milliseconds. In this case, the position hold ends at 3000ms.

Finally, we can do a jump. This is done by executing the force profile set-up earlier using the `ExecuteForceProfile` function. Immediately after, we put the leg into a position ready for touchdown by calling `HoldPosition`.

```c++
leg.ExecuteForceProfile();
leg.HoldPosition(25.0f, 110.0f, true, 800);
```

Since end_at_touchdown is set, the position hold ends at either touchdown or 800ms, whichever comes first.

Finally, we put the leg into a position with enough time for us to secure it before it powers down, so it doesn't crash to the ground.

```c++
leg.HoldPosition(45.0f, 90.0f, false, 3000);
```

We can then request the idle state to end the jump.

```c++
leg.RequestIdleState();
```

### Continuous hopping

With a single jump done, let us try consecutive jumps by typing 'g'. Let us examine this code in detail to see how it is done.

It starts similarly with a single jump by setting the initial phase to `TOUCHDOWN_PHASE` and entering torque control.

```c++
leg.SetCurrentPhase(TOUCHDOWN_PHASE);

if (!leg.EnterTorqueControl()) {
  Serial.println("Aborting.");
  return;
}
```

The initial jump is different in that there is no downward momentum, so we start the initial jump with less impulse compared to the latter jumps.

```c++
leg.UpdateForceProfile(2200.0f, 10.0f, 0.4f);
```

We also set the maximum fx force to be 10N and the fx proportion to be 0.4. This means that the applied force in the x direction is 0.4 times the applied force in the y directions, capped at 10N.

Now, we can perform the initial jump. This is similar to the single jump earlier.

```c++
leg.HoldPosition(25.0f, 110.0f, false, 3000);
leg.ExecuteForceProfile();
leg.HoldPosition(25.0f, 110.0f, true, 800);
```

After this initial jump, we need to update the force profile with a larger impulse, since the leg will be touching down with a downward momentum.

```c++
leg.UpdateForceProfile(2600.0f, 10.0f, 0.4f);
```

Once this is set-up, we can execute multiple jumps in a for loop.

```c++
for (int jump=1; jump<10; jump++) {
  leg.ExecuteForceProfile();
  leg.HoldPosition(25.0f, 110.0f, true, 800);
}
```

At the end of the last jump, we want to end with the raised position with enough time to secure the leg before powering down.

```c++
leg.HoldPosition(45.0f, 90.0f, false, 4000);
```

Finally, we end by putting the leg into the idle state.

```c++
leg.RequestIdleState();
```

## Where to go from here

After going through the OverleapExample sketch, you are already familiar with the core functionality of Overleap and can begin coding your own Overleap controller.

The README of the [Overleap Arduino library](Overleap) lists relevant function declarations and contains detailed comments on their usage.

The framework of using touchdown and takeoff times for calculating the needed impulse to reache a desired height is already set-up, and you can modify the Overleap library for this functionality.

Have fun!

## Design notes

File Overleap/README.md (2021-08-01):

# Overleap Arduino Library

This library is for controlling Overleap with Arduino. The full project can be found at the [Overleap repository](https://github.com/aarondls/overleap).

## Usage

### Structures

There are two structs defined: `MotorTorquePair` and `ForceProfile`.

```c++
struct MotorTorquePair {
  float motor_0;
  float motor_1;
};

struct ForceProfile {
  unsigned long duration; // duration of force in ms
  float a; // amplitude
  float b; // period factor, which is 1000/force duration in ms
  float max_fx_force; // maximum fx force to be applied in N
  float fx_proportion; // proportion of fy force that is applied as fx
};
```

`MotorTorquePair` is used to group together the torque values for both axis, while `ForceProfile` is used to track relevant parameters of the applied force profile.

### Enums

One enum is defined: `Phase`.

```c++
enum Phase {AERIAL_PHASE = 0, TOUCHDOWN_PHASE};
```

This describes the current phase of the leg. `AERIAL_PHASE` is when the leg is in the air and not touching the ground, while `TOUCHDOWN_PHASE` is when the leg is touching the ground. The phase is determined by the custom foot contact sensor.

### Overleap Class

The Overleap class contains several data members and member functions important for controlling Overleap.

```c++
Overleap(float length_0, float length_1, Stream& odrive_serial, Stream& arduino_serial, ODriveArduino& odrive);
```

* This is a constructor that takes in the length of the upper and lower leg as `length_0` and `length_1`, the ODrive and Arduino serial streams, and the ODrive object.

```c++
void SearchEncoderIndex();
```

* This searches for the encoder index signal on both axis, starting with axis 0. There is an intentional slight delay before searching on axis 1. Before calling this function, both the Arduino and ODrive serial ports must have begun. This function is required to run at every start-up to prepare the encoders.

```c++
MotorTorquePair CalculateTorques(float f_x, float f_y);
```

* This calculates needed torque on motors 0 and 1 to achieve desired forces `f_x` and `f_y` on the foot based on current leg position. The calculation is done using transpose of Jacobian. Sign of force directions are with respect to foot: positive x force is to the right while positive y force is downwards, and positive torque is counterclockwise.

```c++
bool LowBatteryVoltage();
```

* This returns true if battery voltage is below 12V. The current voltage is also printed to the Arduino serial monitor.

```c++
bool WithinSafeAngles();
```

* This returns true if current leg position is within safe angles. Safe angles are defined to be between -10 and 75 degrees for θ<sub>0</sub>, and within 0 and 135 degrees for θ<sub>1</sub>.

```c++
bool SafeTorqueDirection(MotorTorquePair torque_pair);
```

* This returns true if torque is in safe direction, even if the leg is not within safe angles. Safe direction is defined to be a value of torque that will not cause the leg to move away from safe angle. This is useful if leg is not within safe angles, but current torque will bring it towards safe angles.
* The direction of torque follows Overleap's direction of torque for both axis: positive torque goes clockwise for axis 0, while positive torque goes counterclockwise for axis 1.

```c++
bool Touchdown();
```

* This returns true if leg is on the ground as detected by the foot contact sensor.

```c++
void UpdateForceProfile(float force_impulse, float fx_max, float fx_proportion);
```

* This updates the force profile member variable with impulse of `force_impulse` in N ms, maximum fx force of `fx_max`, and proportion of fy to be applied as fx of `fx_proportion`.

```c++
void UpdatePhase();
```

* This updates the current phase of the leg as detected by the foot contact sesor.

```c++
bool RequestControlMode(int axis, int requested_control_mode, int timeout=1);
```

* This requests the given control mode. Timeout is in seconds and is approximate. It returns true if sucessful.

```c++
bool RequestAxisState(int axis, int requested_axis_state, int timeout=1);
```

* This requests the given axis state. Timeout is in seconds and is approximate. It returns true if sucessful.

```c++
bool RequestIdleState();
```

* This puts both axis into idle state. It returns true if successful, false if not.

```c++
bool EnterTorqueControl();
```

* Before calling, angles must already be calibrated. This sets the control mode to torque and enters closed loop control for both axis. The initial torque is set to 0. It returns true if successful, false if not.

```c++
void HoldPosition(float pd_0, float pd_1, bool end_at_touchdown, unsigned long duration=10000);
```

* Before calling, leg must be in torque mode and closed loop control. `pd_0` is desired position in degrees for axis 0, while `pd_1` is desired position in degrees for axis 1. `end_at_touchdown` should be set if leg needs to end position hold at touchdown. `duration` is the length of the position hold in milliseconds.
* If `end_at_touchdown` is set, position hold also ends when leg touches the ground. `end_at_touchdown` is also used to determine how "stiff" the position hold is: if ending at touchdown, the gains are less, if not ending at touchdown, then the gains are higher so the leg can support itself
* It ends by commanding zero torque.

```c++
void ExecuteForceProfile();
```

* Before calling, leg must be in torque control mode and closed loop control. This executes the force profile with the set parameters. Execution of force profile stops if foot is no longer on the ground or if force duration is exceeded. It ends by commanding zero torque.

```c++
bool CalibrateAngles();
```

* This calibrates zero angle position for both angles. Upper leg zero angle is taken with respect from the horizontal, while lower leg zero angle is taken with respect from (extending) the upper leg.

```c++
bool CalibratedAngles();
```

* This returns true if angles have been calibrated. This is done by calling the `CalibrateAngles` function.

```c++
void SetCurrentPhase(Phase current_phase);
```

* This sets the current phase of the leg.

```c++
Phase CurrentPhase();
```

* This returns the current phase of the leg.

```c++
void PrintLegPosVel();
```

* This prints the current position and velocity of both axis, as well as if angles are within safe position, to the Arduino serial monitor in one line.

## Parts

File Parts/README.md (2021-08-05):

# Parts

## Off the shelf

* [ODrive Motor Controller](https://odriverobotics.com/shop/odrive-v36)
    * 24V with connectors
* [T-Motor Antigravity 4006 380KV - 2 pcs](https://store.tmotor.com/goods.php?id=440)
* [Teensy 3.6 Microcontroller](https://www.pjrc.com/store/teensy36.html)
    * Any Arduino-compatible microcontroller works as well
* [AS5047 Magnetic Encoder Eval Board](https://www.digikey.com/en/products/detail/ams/AS5047P-TS-EK-AB/5452344) - 2 pcs
* Male to Female 20cm length Jumper Wires
    * There are many packs of these
* [Force Sensitive Resistor](https://buyinterlinkelectronics.com/collections/new-standard-force-sensors/products/copy-of-fsr-model-408-100mm-length)
* Rubber sheet 1/8" thick
    * Any size/roll can be used as they will be cut to size
* [GT3 3mm pitch 6mm width timing belt](https://shop.sdp-si.com/catalog?cid=p342)
    * 2 pcs 63T
    * 1 pc 70T
    * 1 pc 125T
* 6706-2RS Bearing - 2 pcs
* MR84-ZZ Bearing - 6 pcs
* 4mm diameter aluminum rod
    * There are many packs of >10cm which you can cut to size.
* M2.5 Countersunk Screws
    * 4mm, 5mm, 6mm, 8mm, 10mm, 12mm, 18mm, 25mm lengths
    * All screws except 25mm length will need at least 20pcs. A set of assorted screws such as [these](https://www.amazon.com/Guard4U-Stainless-Phillips-Countersunk-Assortment/dp/B08LXFBB3M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) could work, or each can be sourced individually.
* M2.5 Tapered Heat Set Inserts
    * [These ones](https://www.mcmaster.com/catalog/127/3569) from McMaster-Carr work well. There are also other options on Amazon and the like.
* 3/4" Aluminum square tube
    * 48" length tubes are available at hardware stores. These can be cut to size with a hacksaw. Length doesn't have to be extremely precise.
* 1/4" Nuts, Washers, and Hex Bolts
    * Assorted lengths are available at hardware stores. Length does not need to be exact and can be changed depending on what is available. These are used only for the 2 DOF rotating base.
* Presswood
    * Any material for the base of the rotating arm will do nicely.

## 3D Printed

All parts can be printed at 20% infill with PLA filament. ABS/Nylon can also be used if your printer supports it.

* Motor 0 Bracket - 1x
* M0 Encoder Cover - 1x
* Pulley Coupler - 2x
* 16T Pulley - 2x
* 16T Cover - 2x
* Compound 16T Pulley - 2x
* Compound 48T Pulley - 2x
* Compound 48T Cover - 2x
* 6706 Bearing Housing - 2x
* 6706 Bearing Lock - 2x
* Hip 48T Pulley- 1x
* Hip 48T Cover - 1x
* M1 Coupler - 1x
* M1 Bracket - 1x
* M1 Encoder Cover - 1x
* Upper Leg Coupler - 1x
* MR84 Bearing Housing - 2x
* Top Plate - 1x
* Inner Upper Leg - 1x
* Outer Upper Leg - 1x
* Knee 48T Pulley - 1x
* Outer Lower Leg - 1x
* Inner Lower Leg - 1x
* Spacer - 1x
* Outer Foot Brace - 1x
* Inner Foot Brace - 1x
* Base Support - 1x
* Leg Connector - 1x
* Rotating Base - 1x
* Top Support - 1x

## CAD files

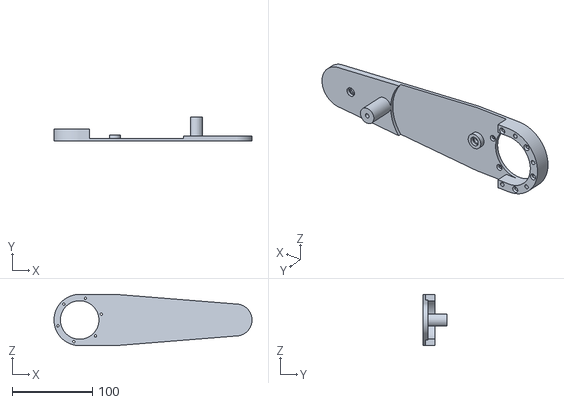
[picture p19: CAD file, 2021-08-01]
Parts/Inner Upper Leg.stl
247.0 x 30.0 x 64.0

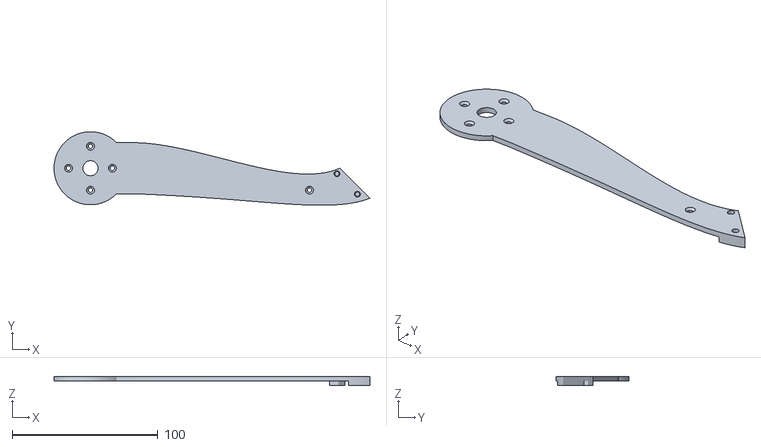
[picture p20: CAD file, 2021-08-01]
Parts/Outer Lower Leg.stl
216.5 x 50.3 x 6.25

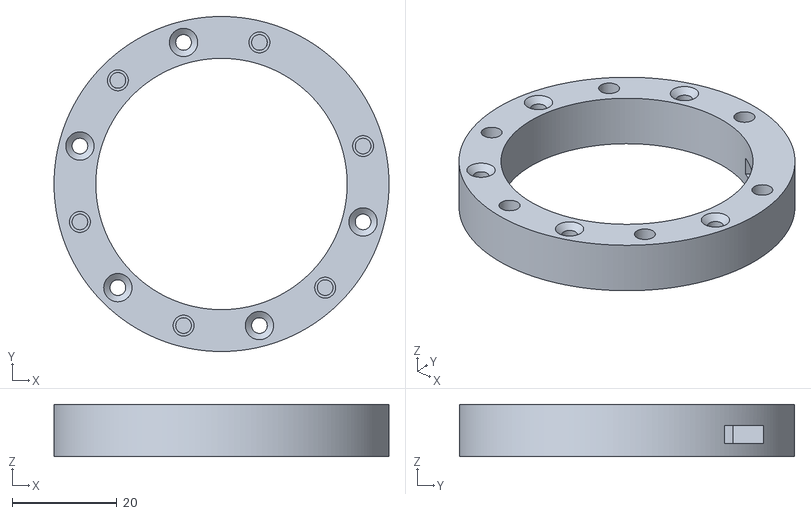
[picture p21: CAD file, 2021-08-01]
Parts/Upper Leg Coupler.stl
64.0 x 64.0 x 10.0

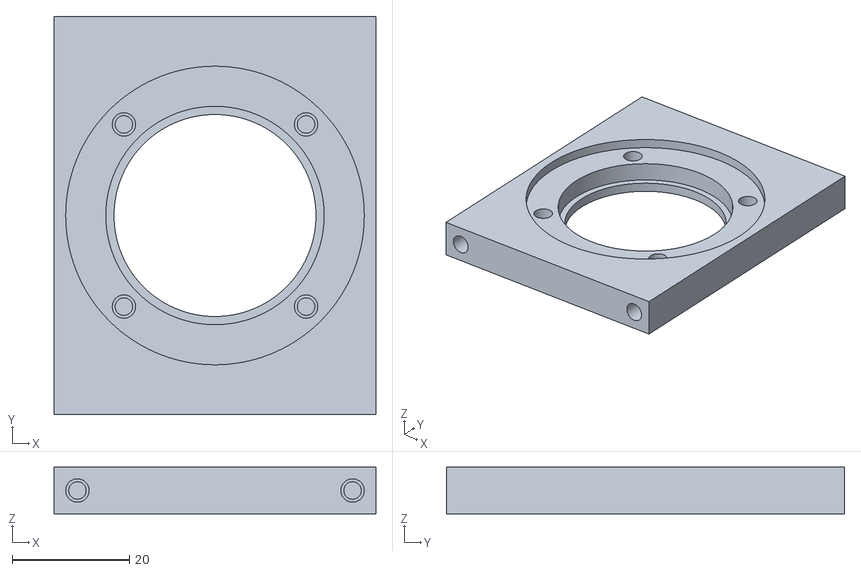
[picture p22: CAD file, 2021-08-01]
Parts/6706 Bearing Housing.stl
55.0 x 68.0 x 8.00

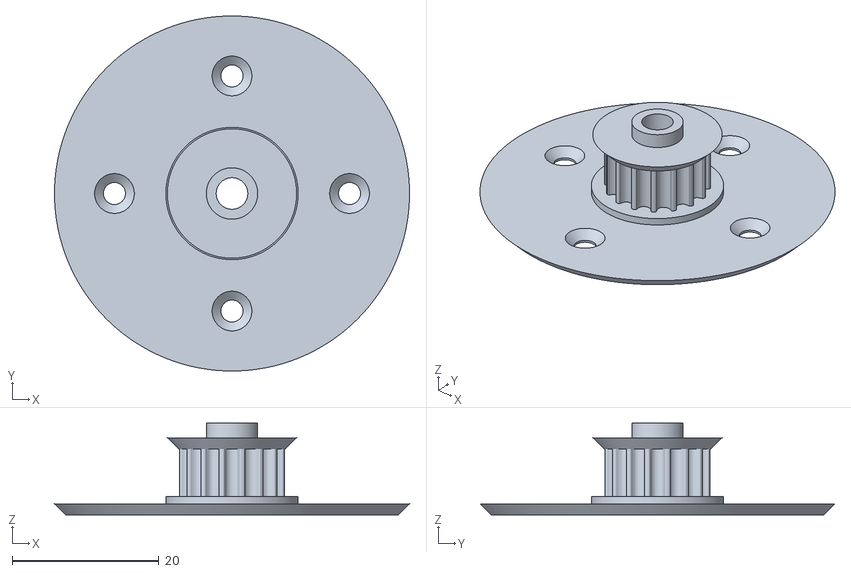
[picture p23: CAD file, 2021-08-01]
Parts/Compound 16T Pulley.stl
48.3 x 48.3 x 12.5

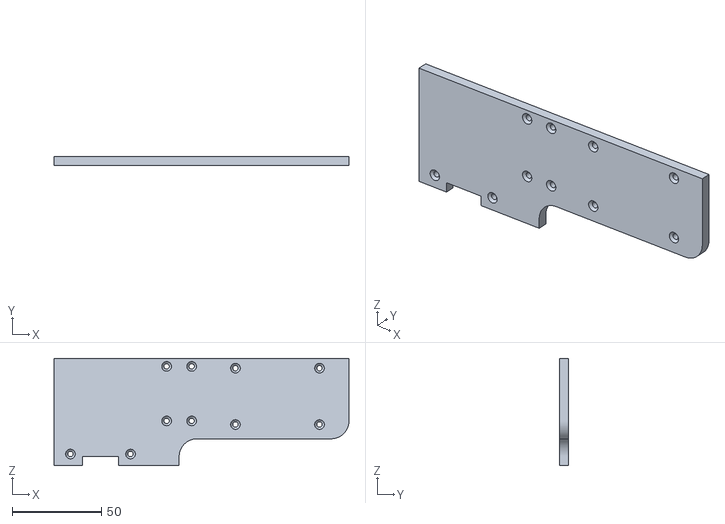
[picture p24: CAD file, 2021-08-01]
Parts/Top Plate.stl
165.0 x 5.00 x 60.0

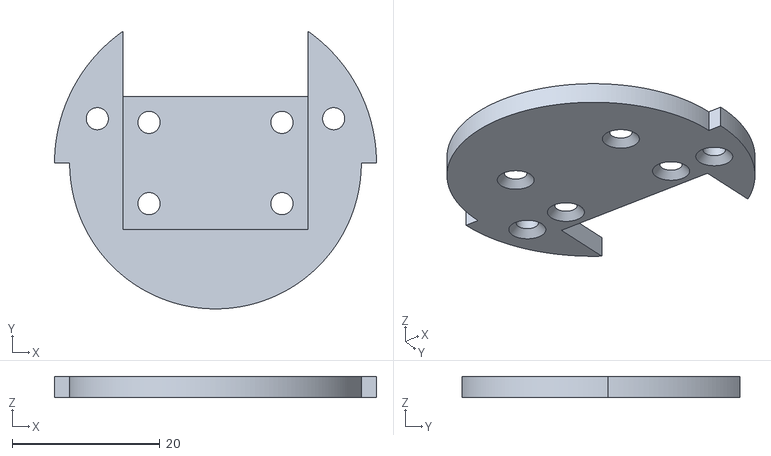
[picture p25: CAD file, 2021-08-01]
Parts/M1 Encoder Cover.stl
43.6 x 37.6 x 2.90

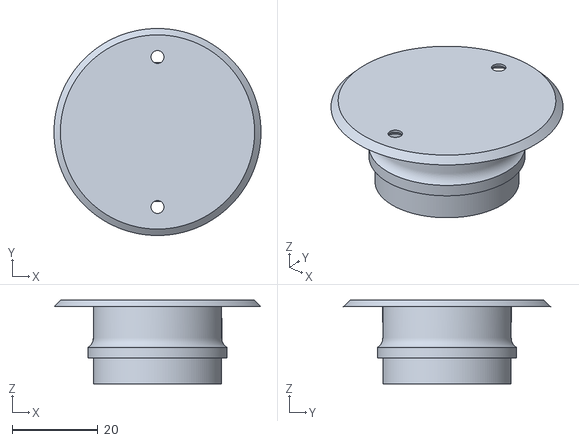
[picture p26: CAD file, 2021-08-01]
Parts/Hip 48T Cover.stl
48.3 x 48.3 x 19.5

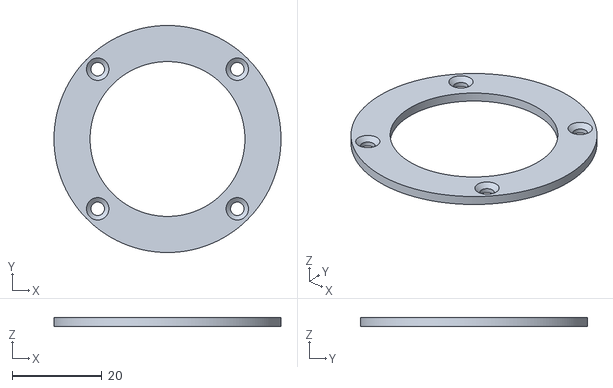
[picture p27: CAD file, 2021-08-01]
Parts/6706 Bearing Lock.stl
50.6 x 50.6 x 1.90

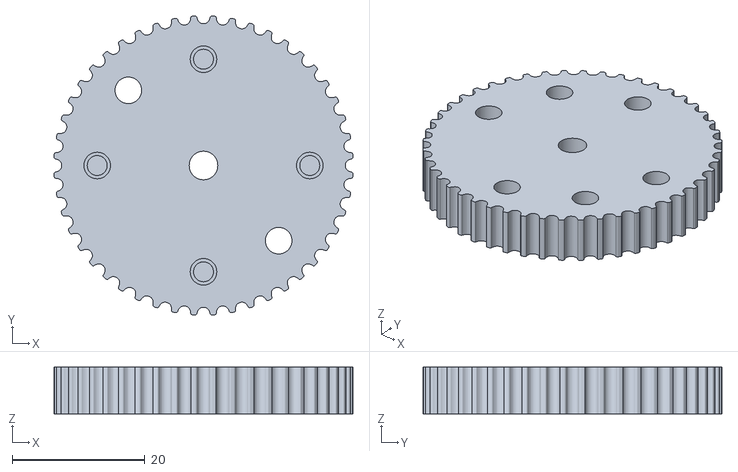
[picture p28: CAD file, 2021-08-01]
Parts/Compound 48T Pulley.stl
45.0 x 45.0 x 7.00

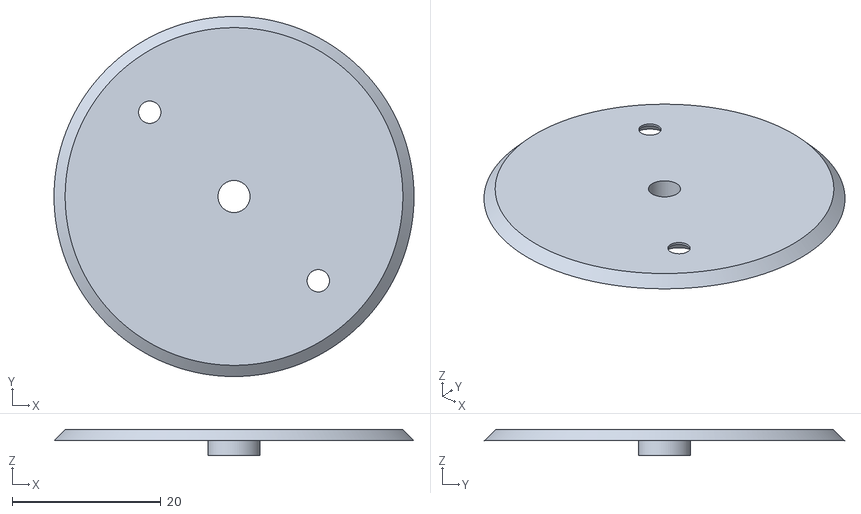
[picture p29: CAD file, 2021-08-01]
Parts/Compound 48T Cover.stl
48.3 x 48.3 x 3.50

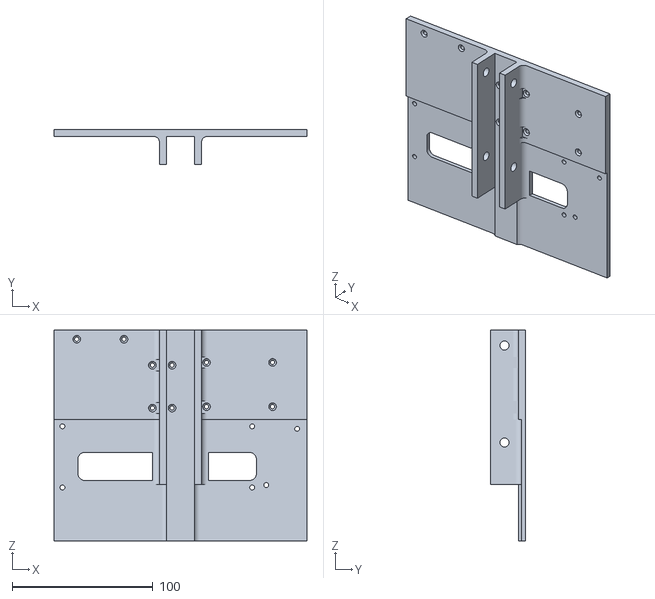
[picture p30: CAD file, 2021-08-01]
Parts/Leg Connector.stl
180.0 x 25.0 x 150.0

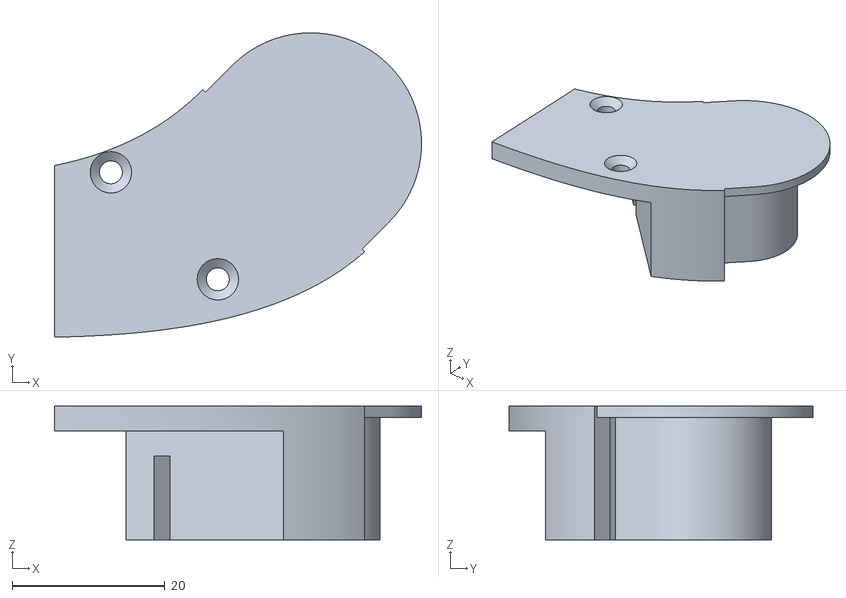
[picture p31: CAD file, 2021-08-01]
Parts/Outer foot brace.stl
48.0 x 39.8 x 17.5

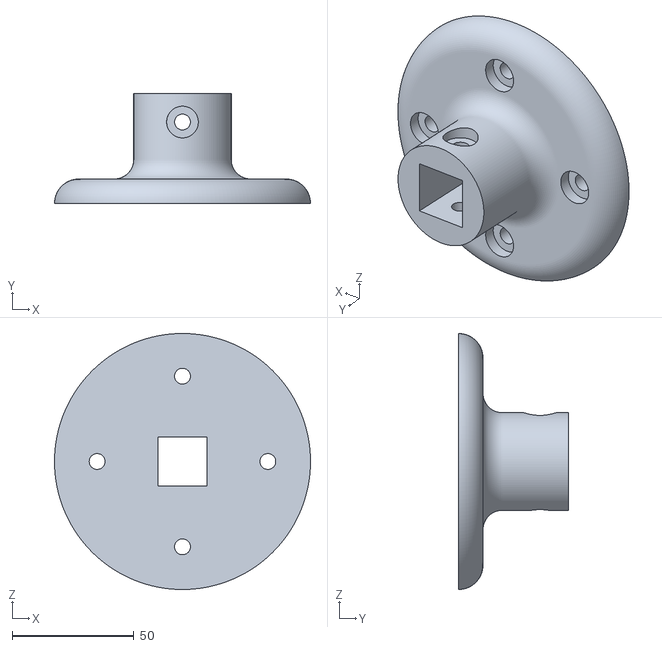
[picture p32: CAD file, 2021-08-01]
Parts/Base Support.stl
105.0 x 45.0 x 105.0

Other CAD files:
Parts/16T Pulley.stl
Parts/Hip 48T Pulley.stl
Parts/Motor 0 Bracket.stl
Parts/M1 Coupler.stl
Parts/16T Cover.stl
Parts/Inner Lower Leg.stl
Parts/Inner foot brace.stl
Parts/Knee 48T Pulley.stl
Parts/M0 Encoder Cover.stl
Parts/M1 Bracket.stl
Parts/MR84 Bearing Housing.stl
Parts/Outer Upper Leg.stl
Parts/Pulley Coupler.stl
Parts/Rotating Base.stl
Parts/Spacer.stl
Parts/Top Support.stl

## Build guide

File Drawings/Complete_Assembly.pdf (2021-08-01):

A

2 | 3 | 4 | 5 | 6 | 7 | 8

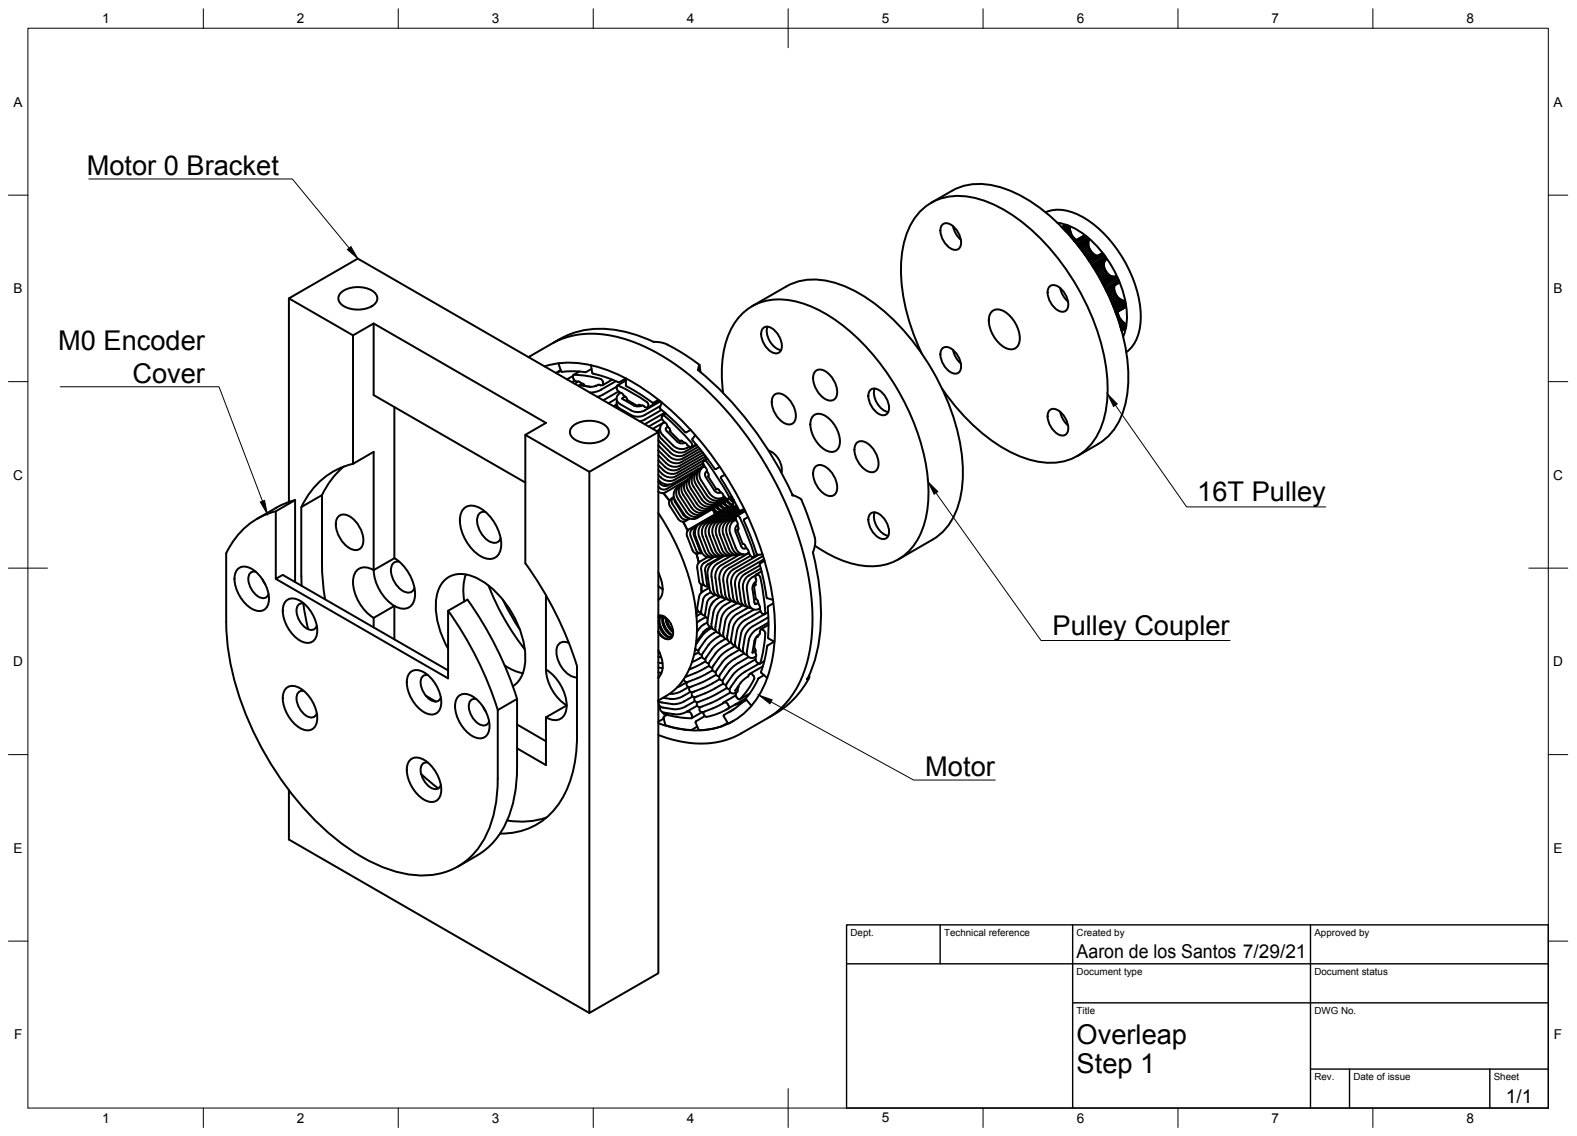
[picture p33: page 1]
Dept.; Technical reference; Created by; Approved by; Document type; Document status; Title; DWG No.; Rev.; Date of issue; Sheet; Step 1; Overleap; 16T Pulley; Motor 0 Bracket; M0 Encoder Cover; Motor; Pulley Coupler

Aaron de los Santos

A

A

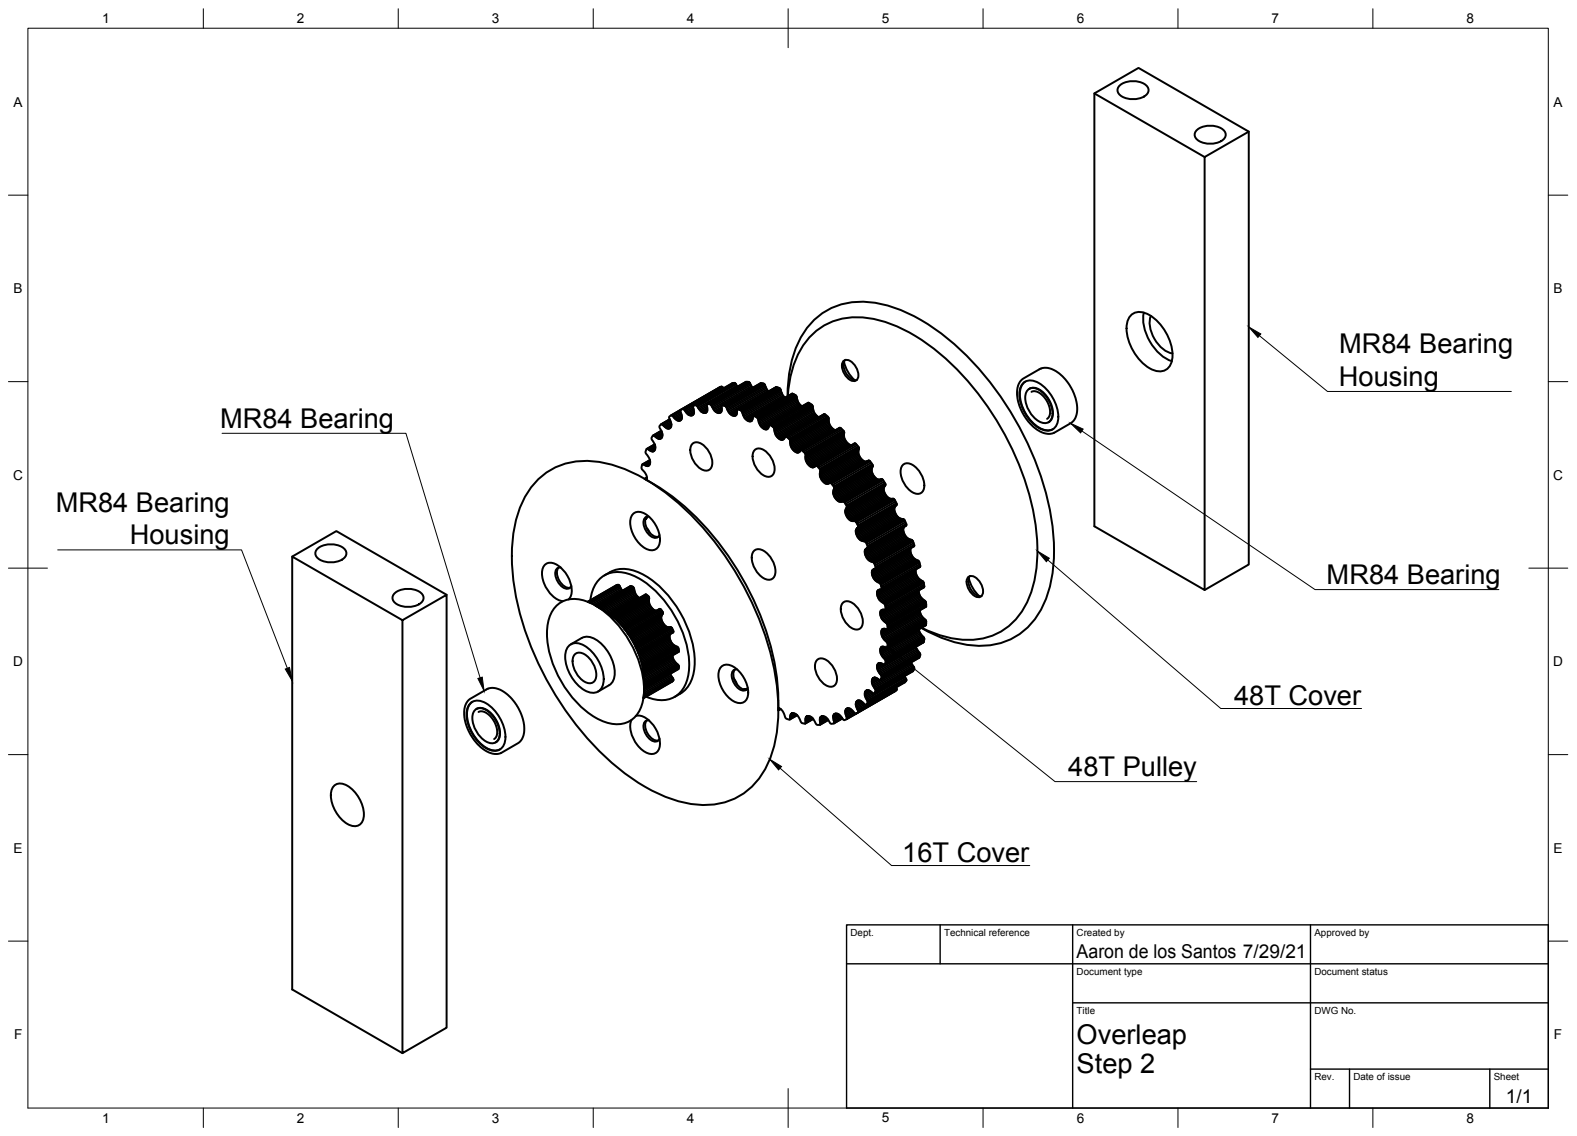
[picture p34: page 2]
Dept.; Technical reference; Created by; Approved by; Document type; Document status; Title; DWG No.; Step 2; Overleap; MR84 Bearing Housing; MR84 Bearing; 48T Cover; 48T Pulley; 16T Cover

Aaron de los Santos

A

A

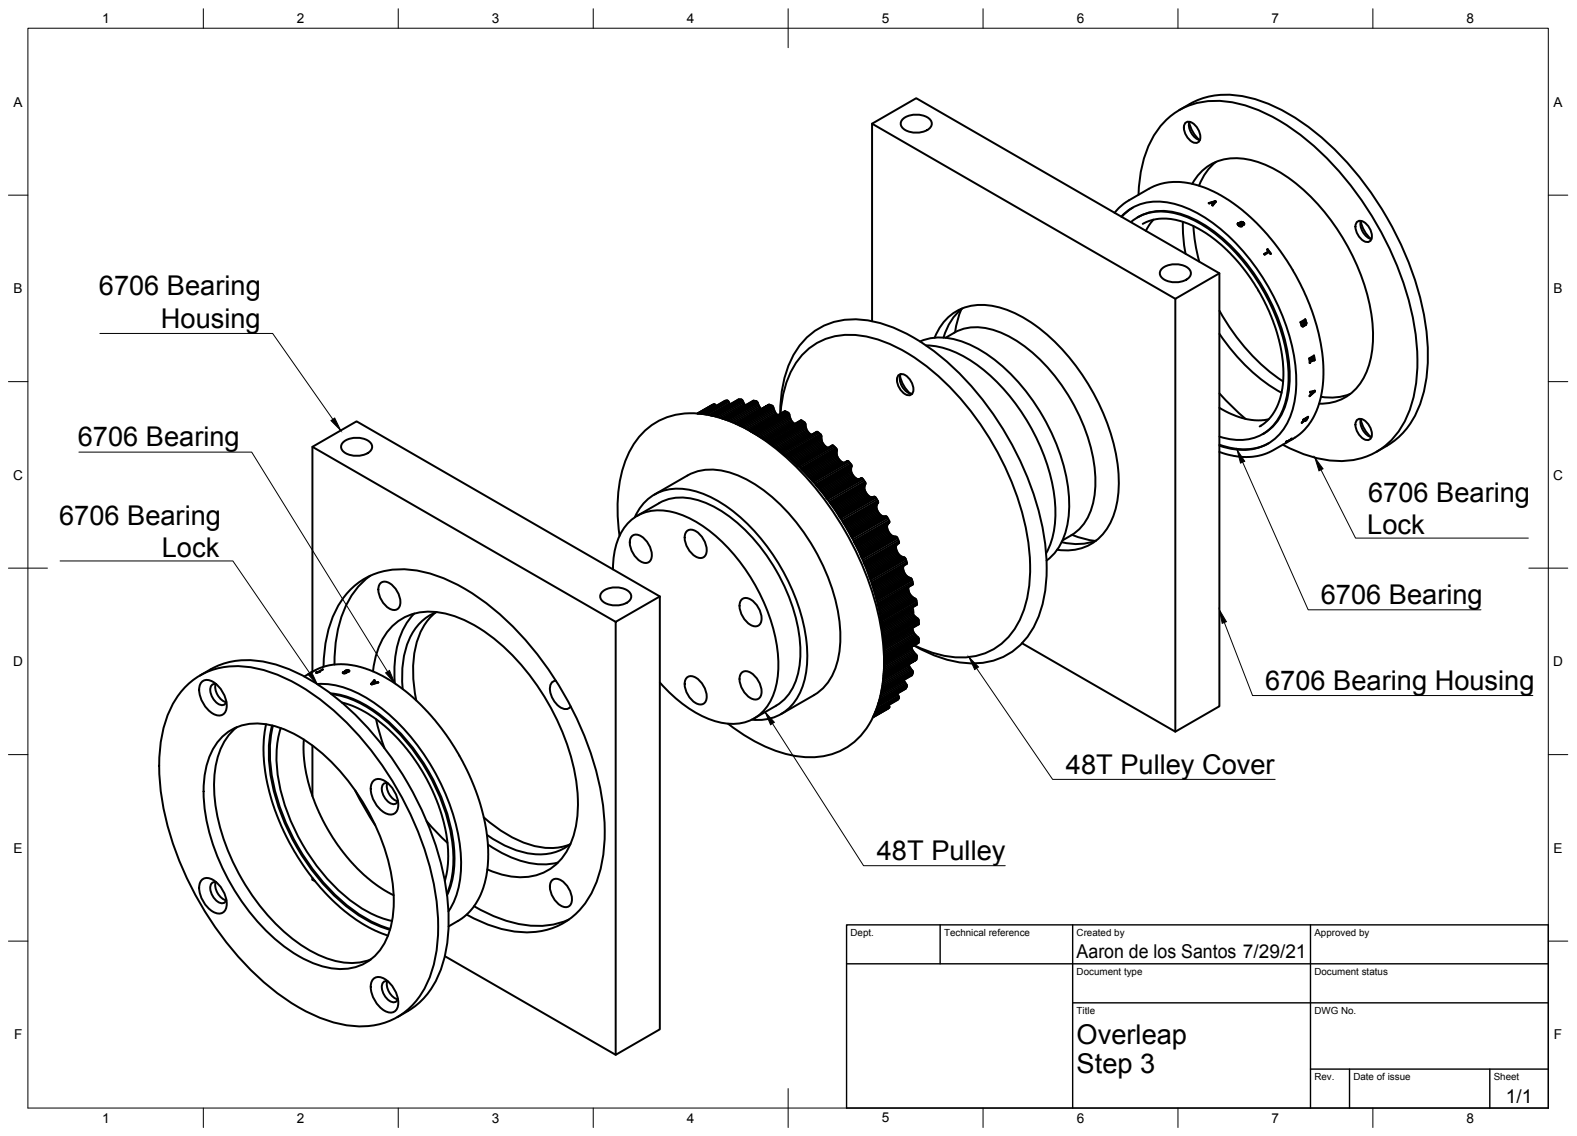
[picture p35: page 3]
Dept.; Technical reference; Created by; Approved by; Document type; Document status; Title; DWG No.; Step 3; Overleap; 6706 Bearing; 6706 Bearing Lock; 6706 Bearing Housing; 48T Pulley; 48T Pulley Cover

Aaron de los Santos

A

A

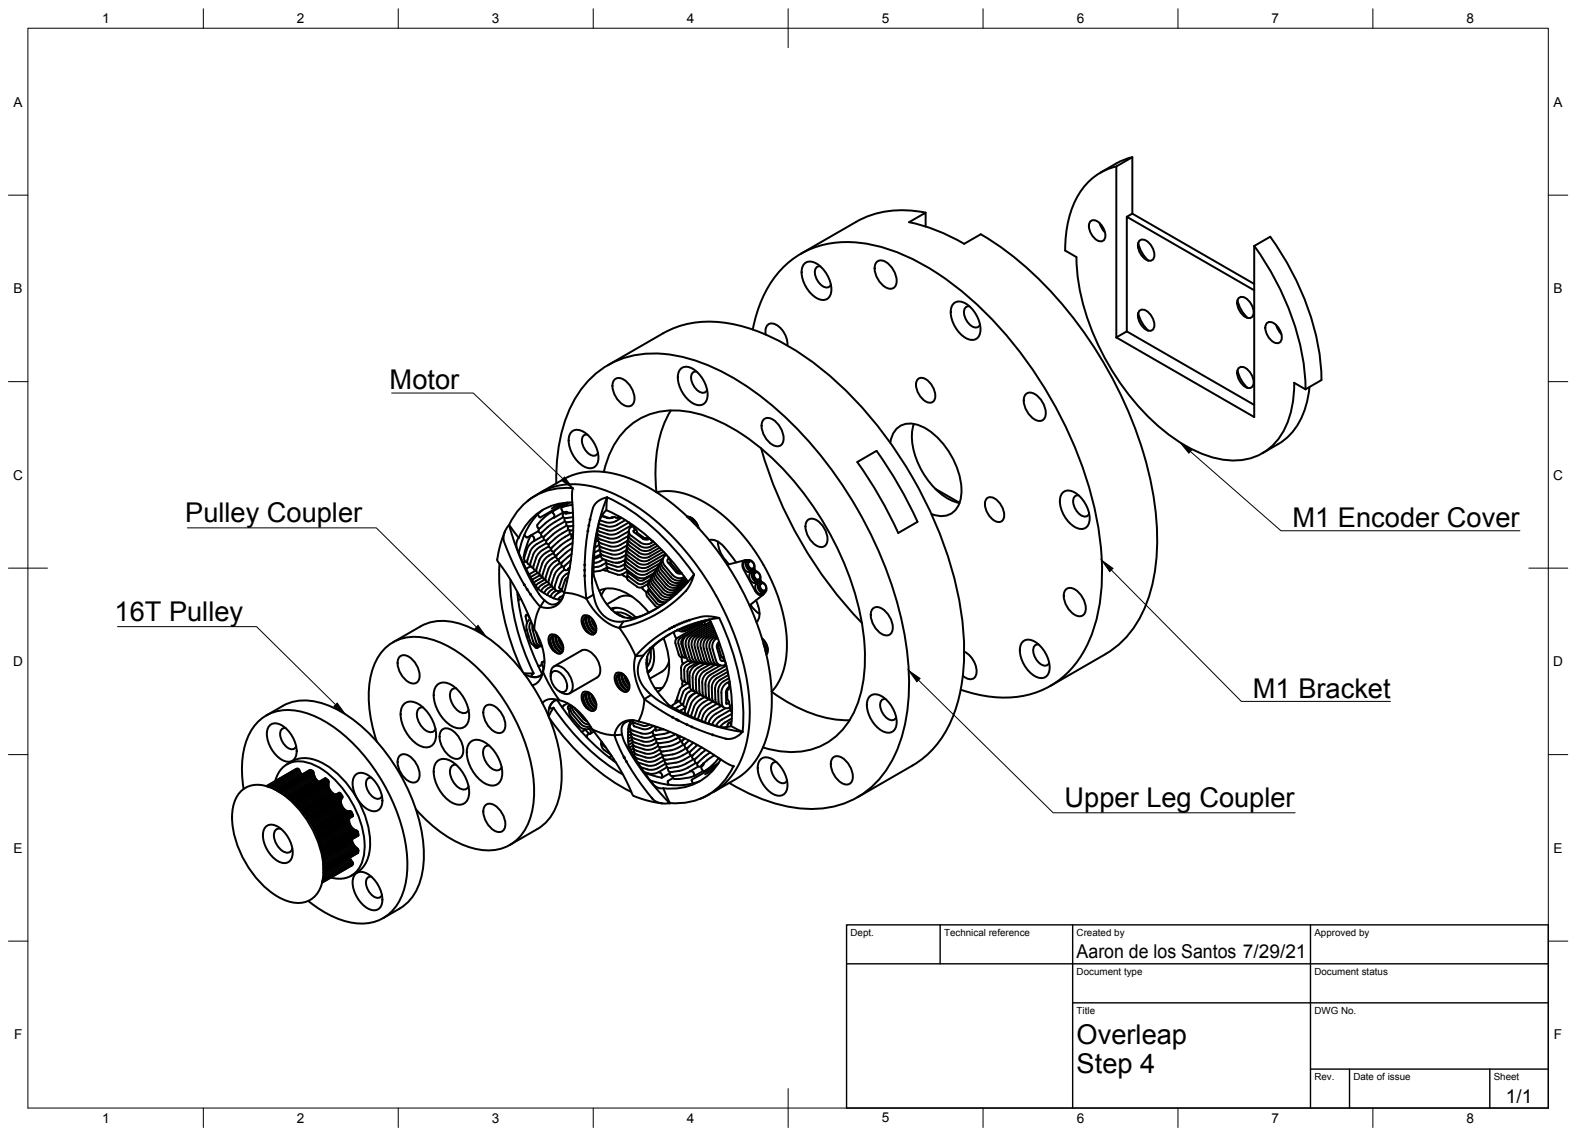
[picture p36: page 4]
Dept.; Technical reference; Created by; Approved by; Document type; Document status; Title; DWG No.; Step 4; Overleap; M1 Bracket; M1 Encoder Cover; 16T Pulley; Pulley Coupler; Motor

Upper Leg Coupler

Aaron de los Santos

A

A

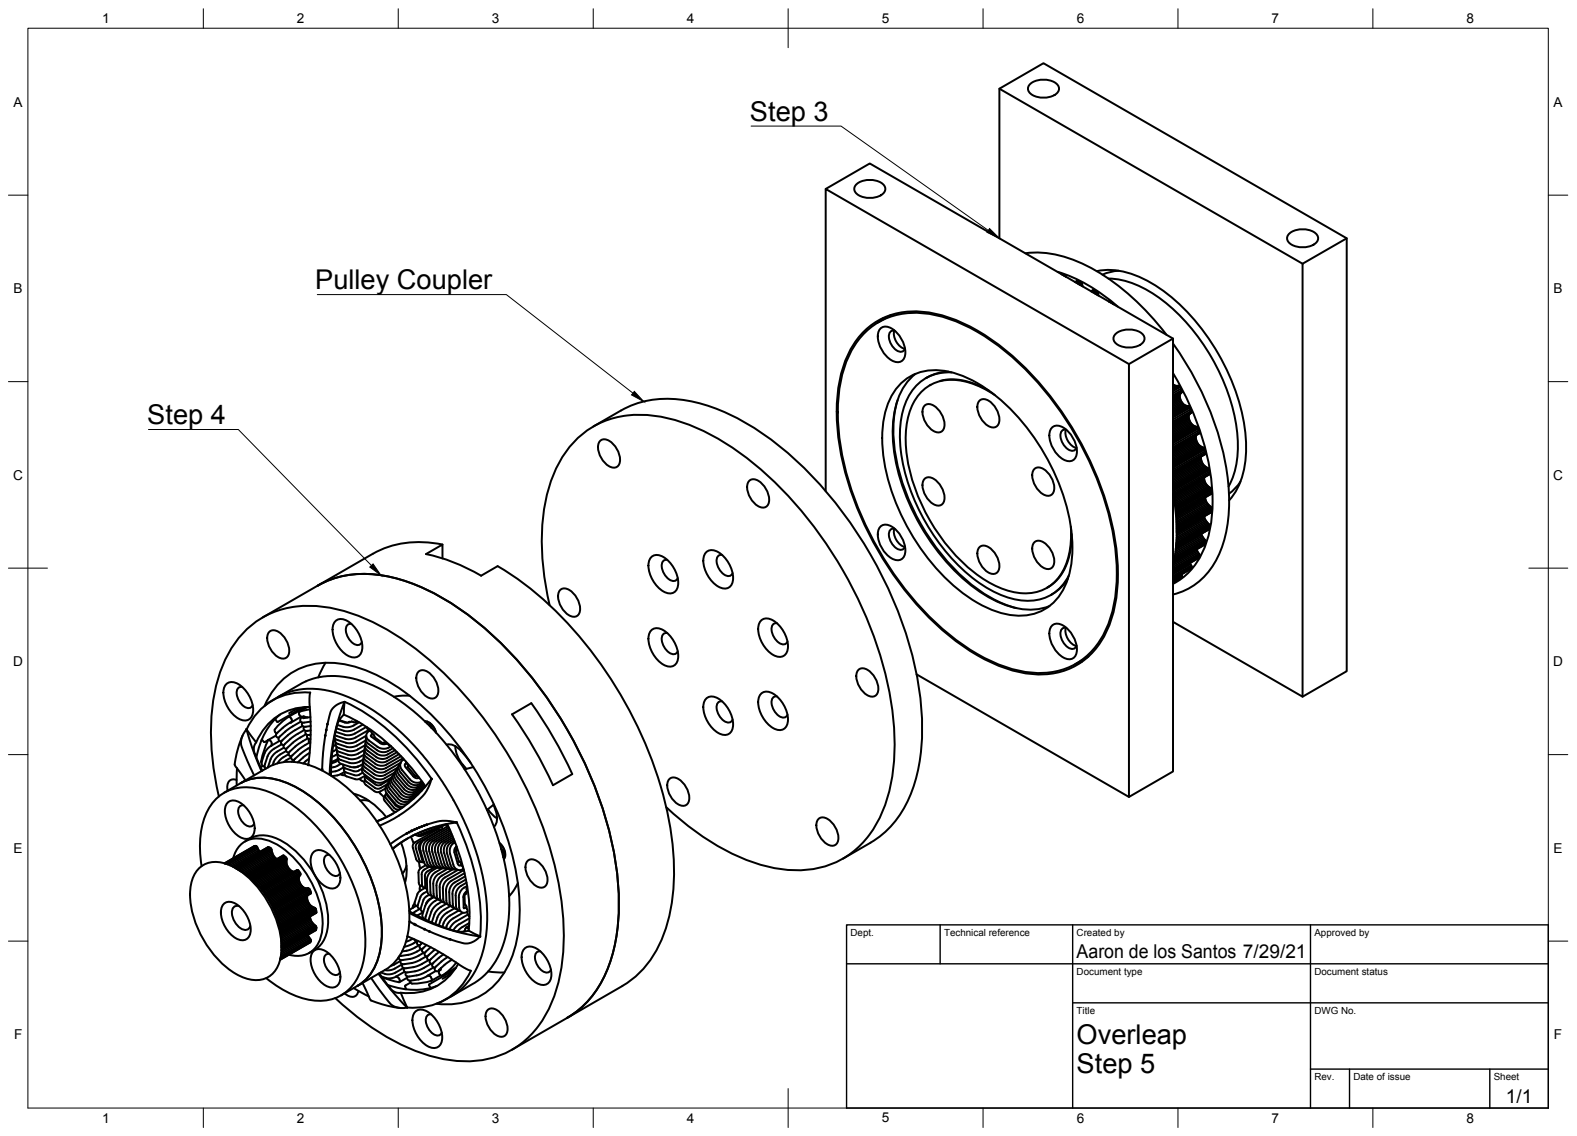
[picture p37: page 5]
Dept.; Technical reference; Created by; Approved by; Document type; Document status; Title; DWG No.; Step 5; Overleap; Pulley Coupler; Step 3; Step 4

Aaron de los Santos

A

A

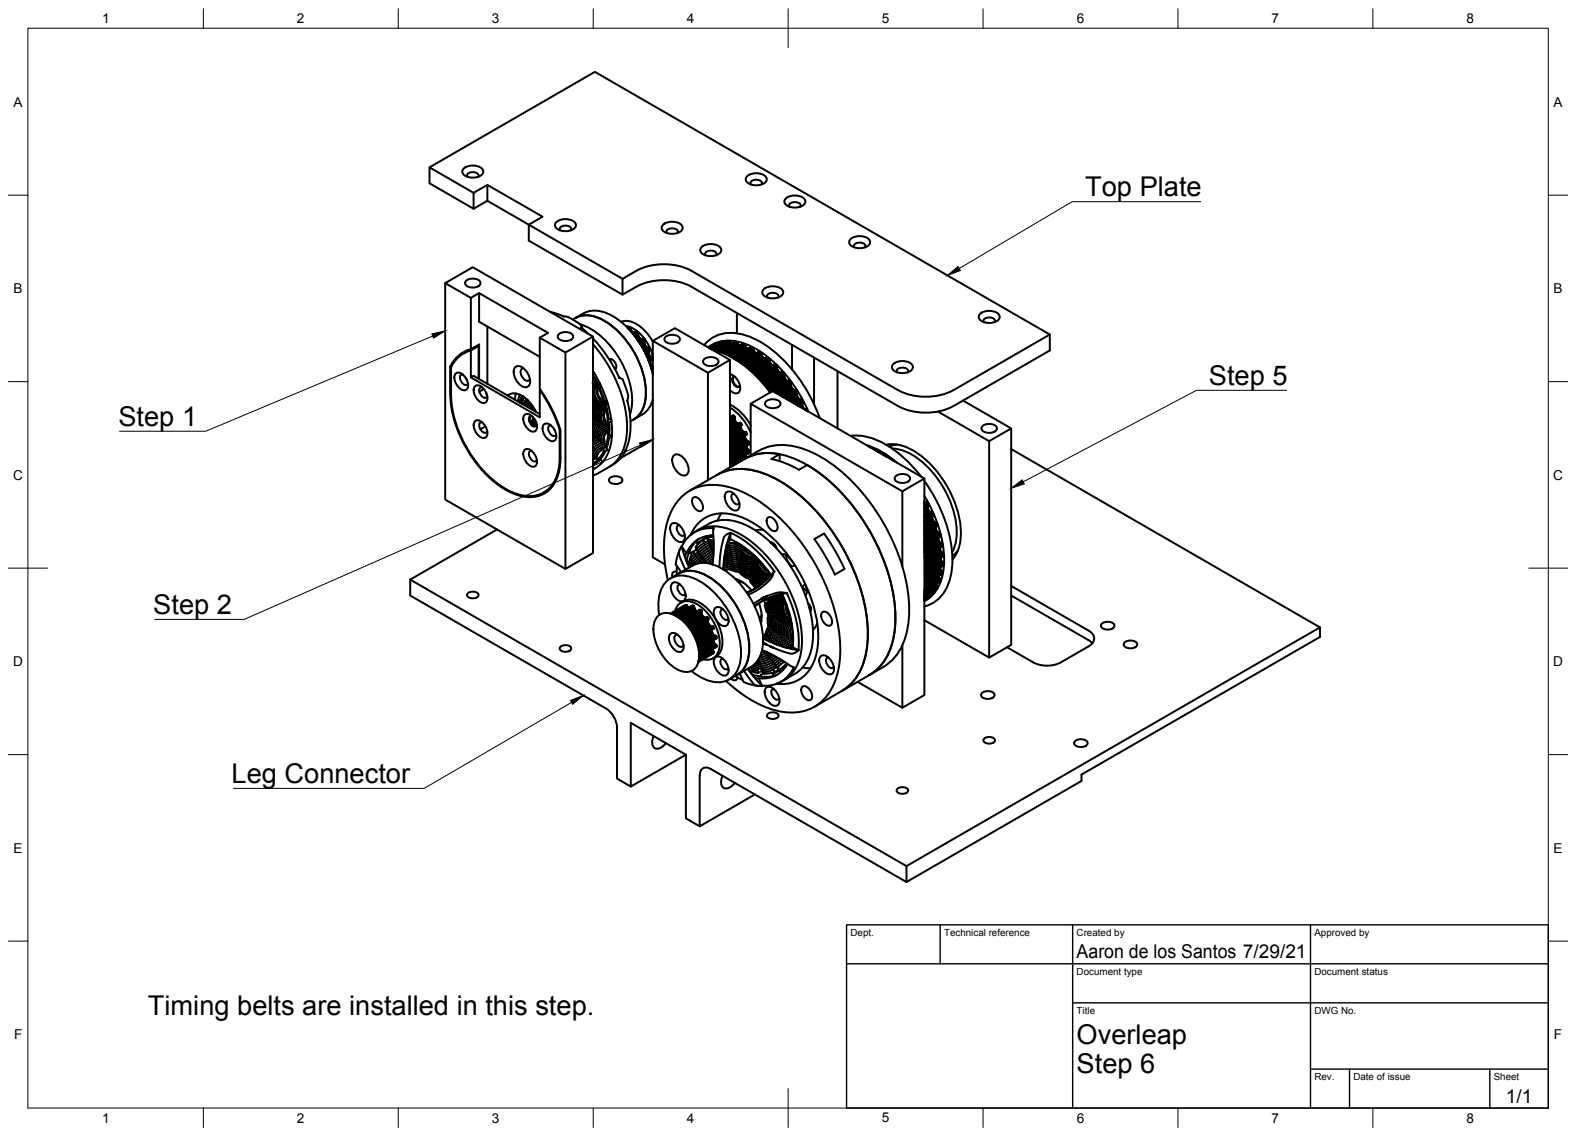
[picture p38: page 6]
Dept.; Technical reference; Created by; Approved by; Document type; Document status; Title; DWG No.; Step 6; Overleap; Leg Connector; Top Plate; Step 2; Step 1; Step 5

Aaron de los Santos

Timing belts are installed in this step.

A

A

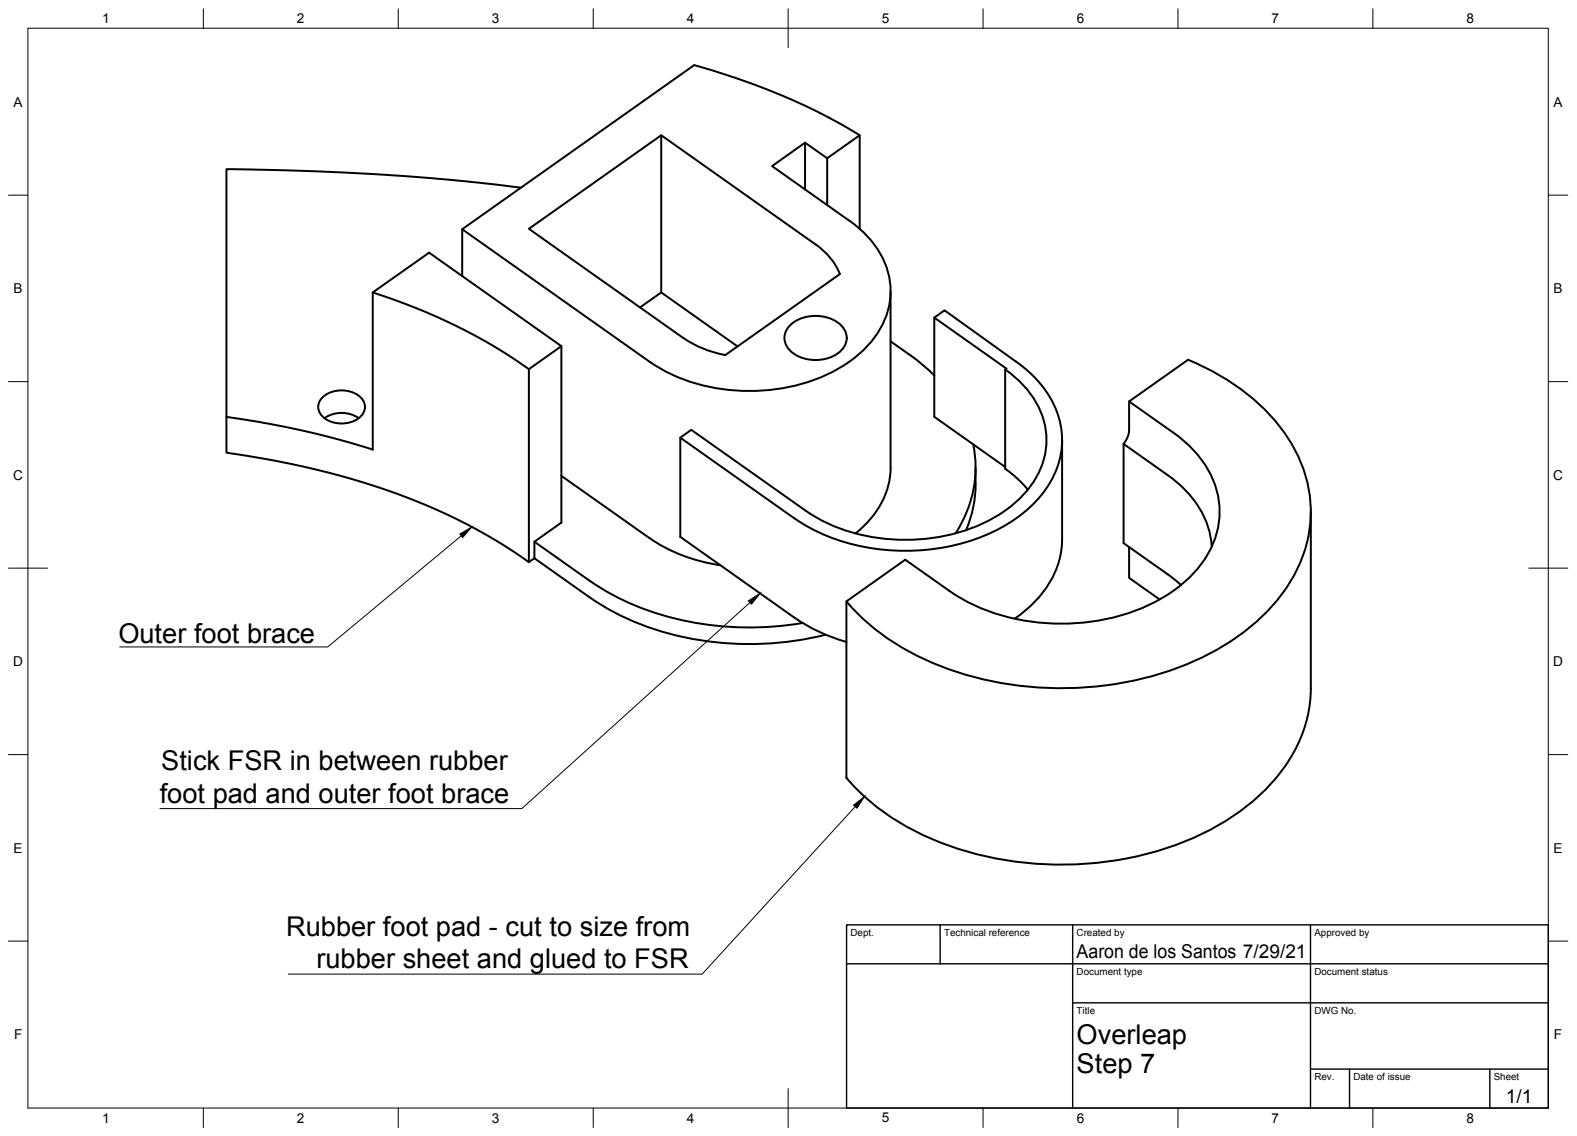
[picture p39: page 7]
Dept.; Technical reference; Created by; Approved by; Document type; Document status; Title; DWG No.; Step 7; Overleap

Outer foot brace

Stick FSR in between rubber
foot pad and outer foot brace

Rubber foot pad - cut to size from
rubber sheet and glued to FSR

Aaron de los Santos

A

A

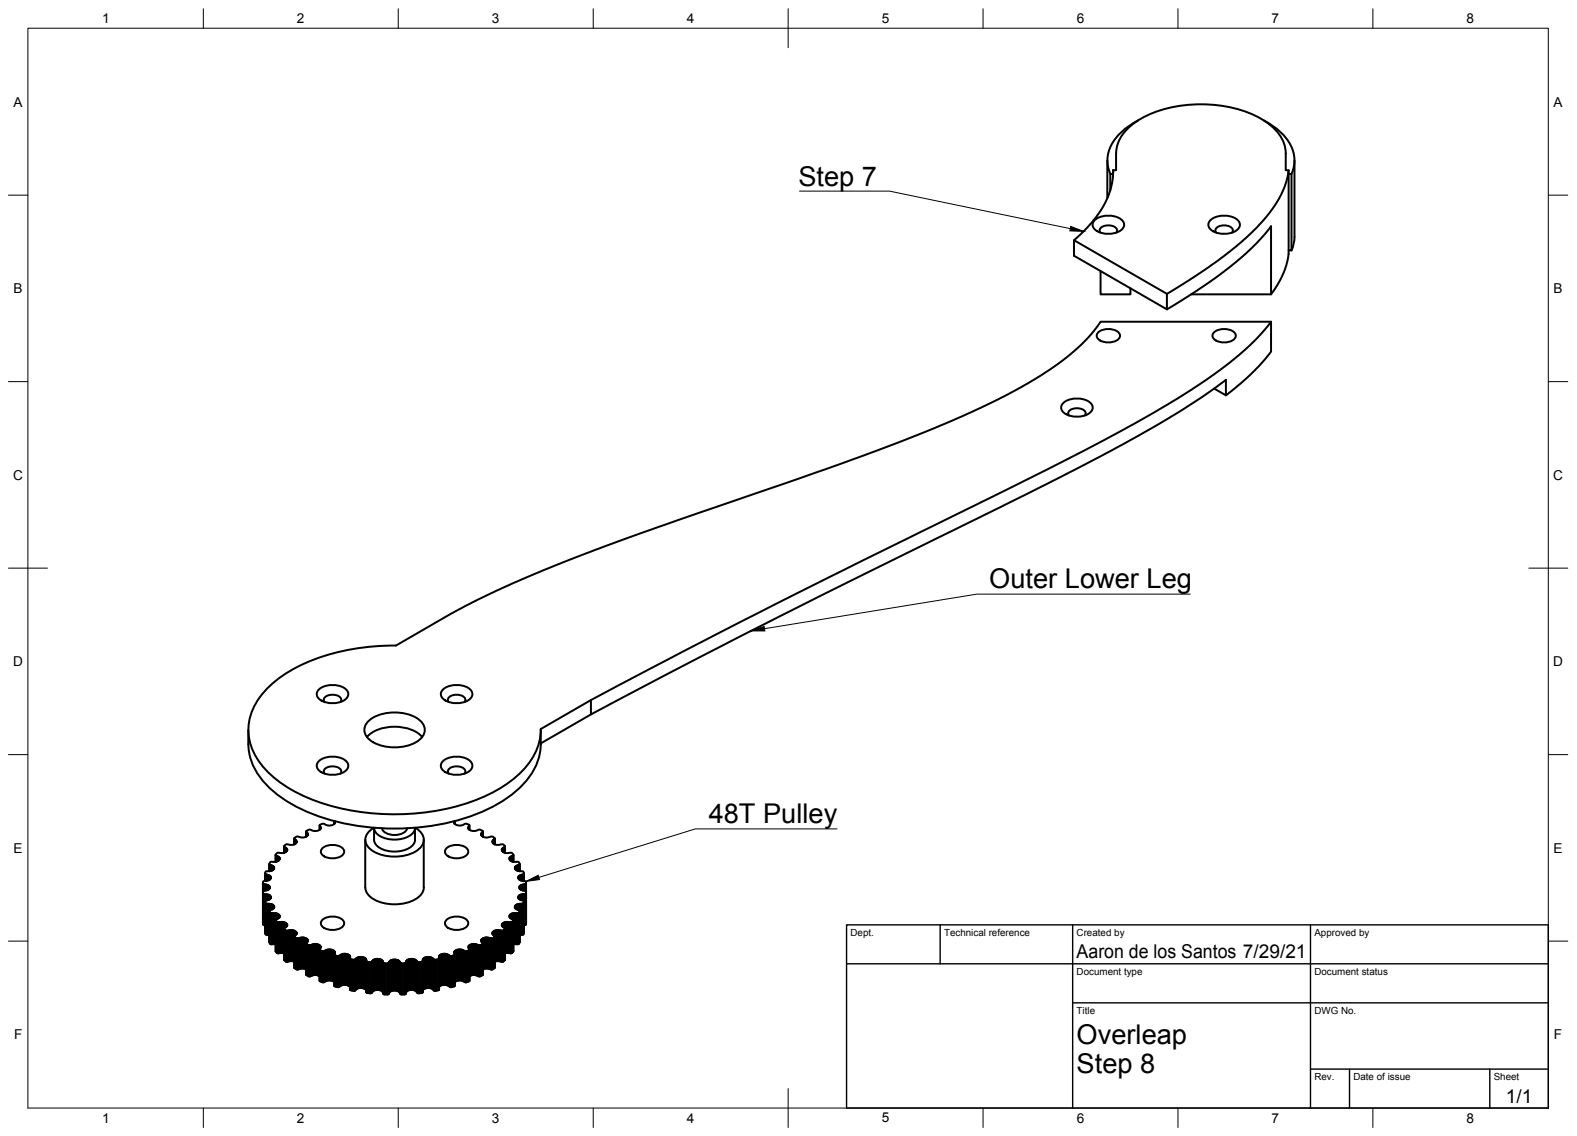
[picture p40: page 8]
Dept.; Technical reference; Created by; Approved by; Document type; Document status; Title; DWG No.; Step 8; Overleap; 48T Pulley; Step 7

Outer Lower Leg

Aaron de los Santos

A

A

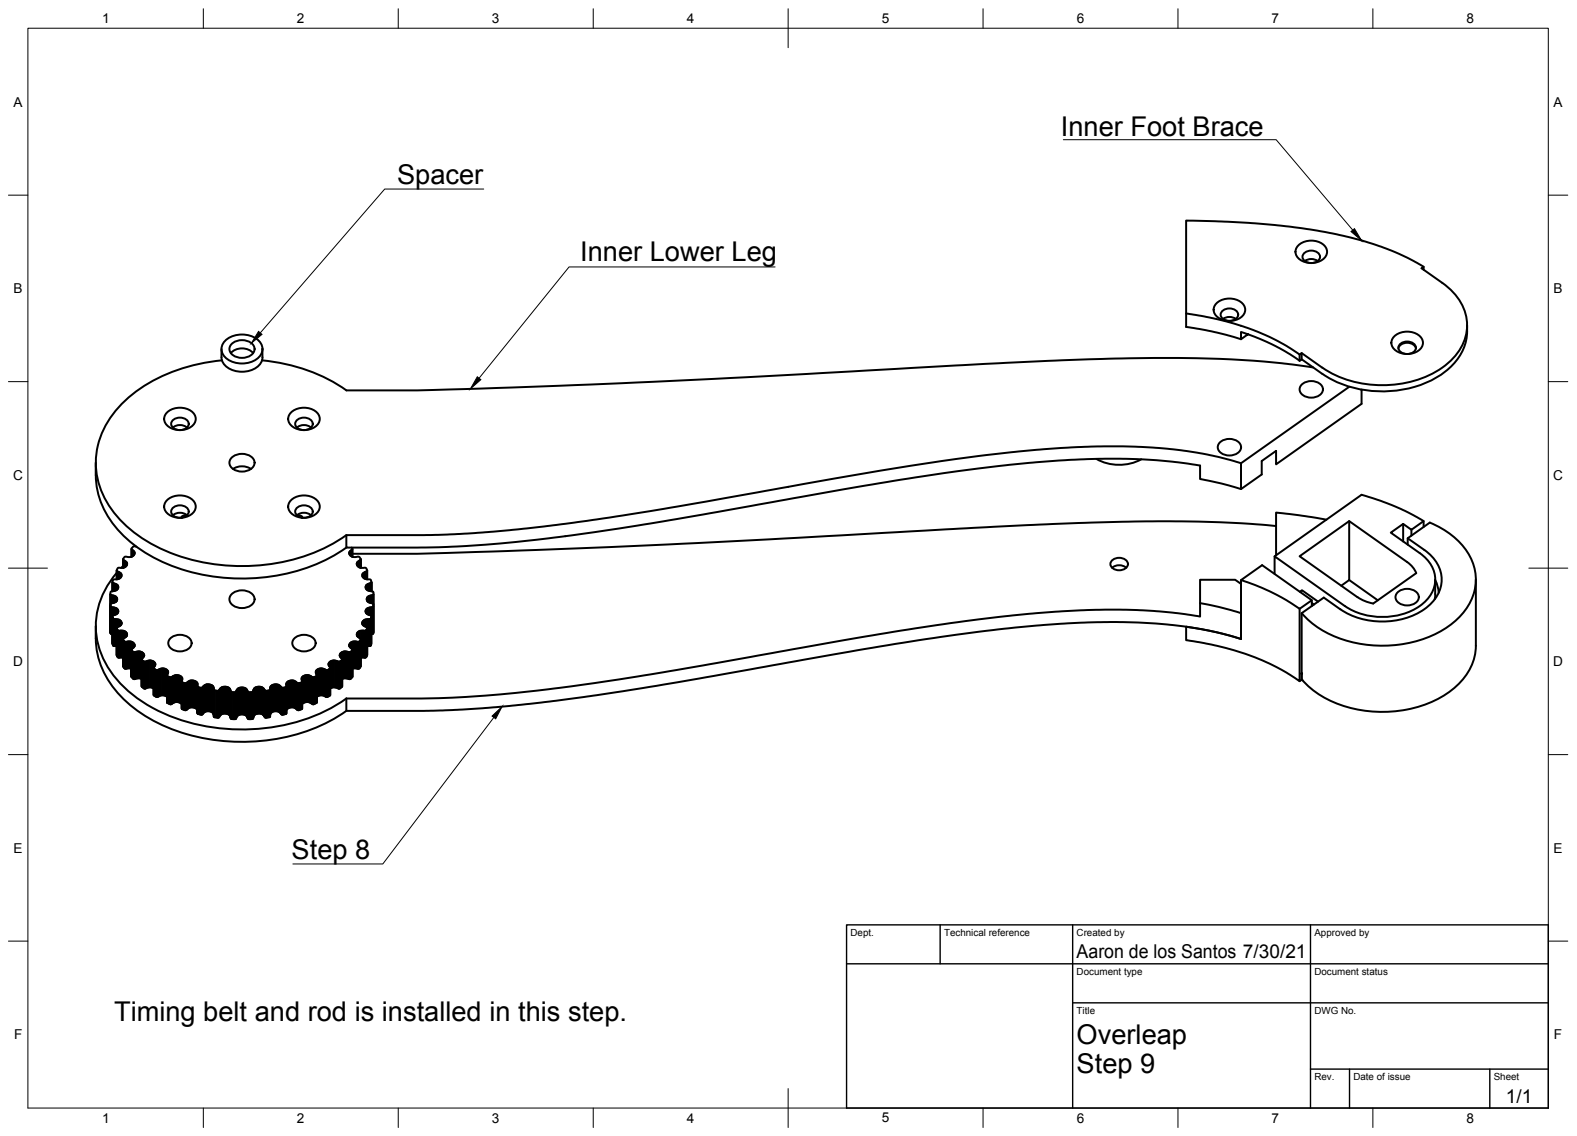
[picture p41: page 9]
Dept.; Technical reference; Created by; Approved by; Document type; Document status; Title; DWG No.; Step 9; Overleap; Spacer; Step 8

Inner Foot Brace

Inner Lower Leg

Aaron de los Santos

Timing belt and rod is installed in this step.

A

A

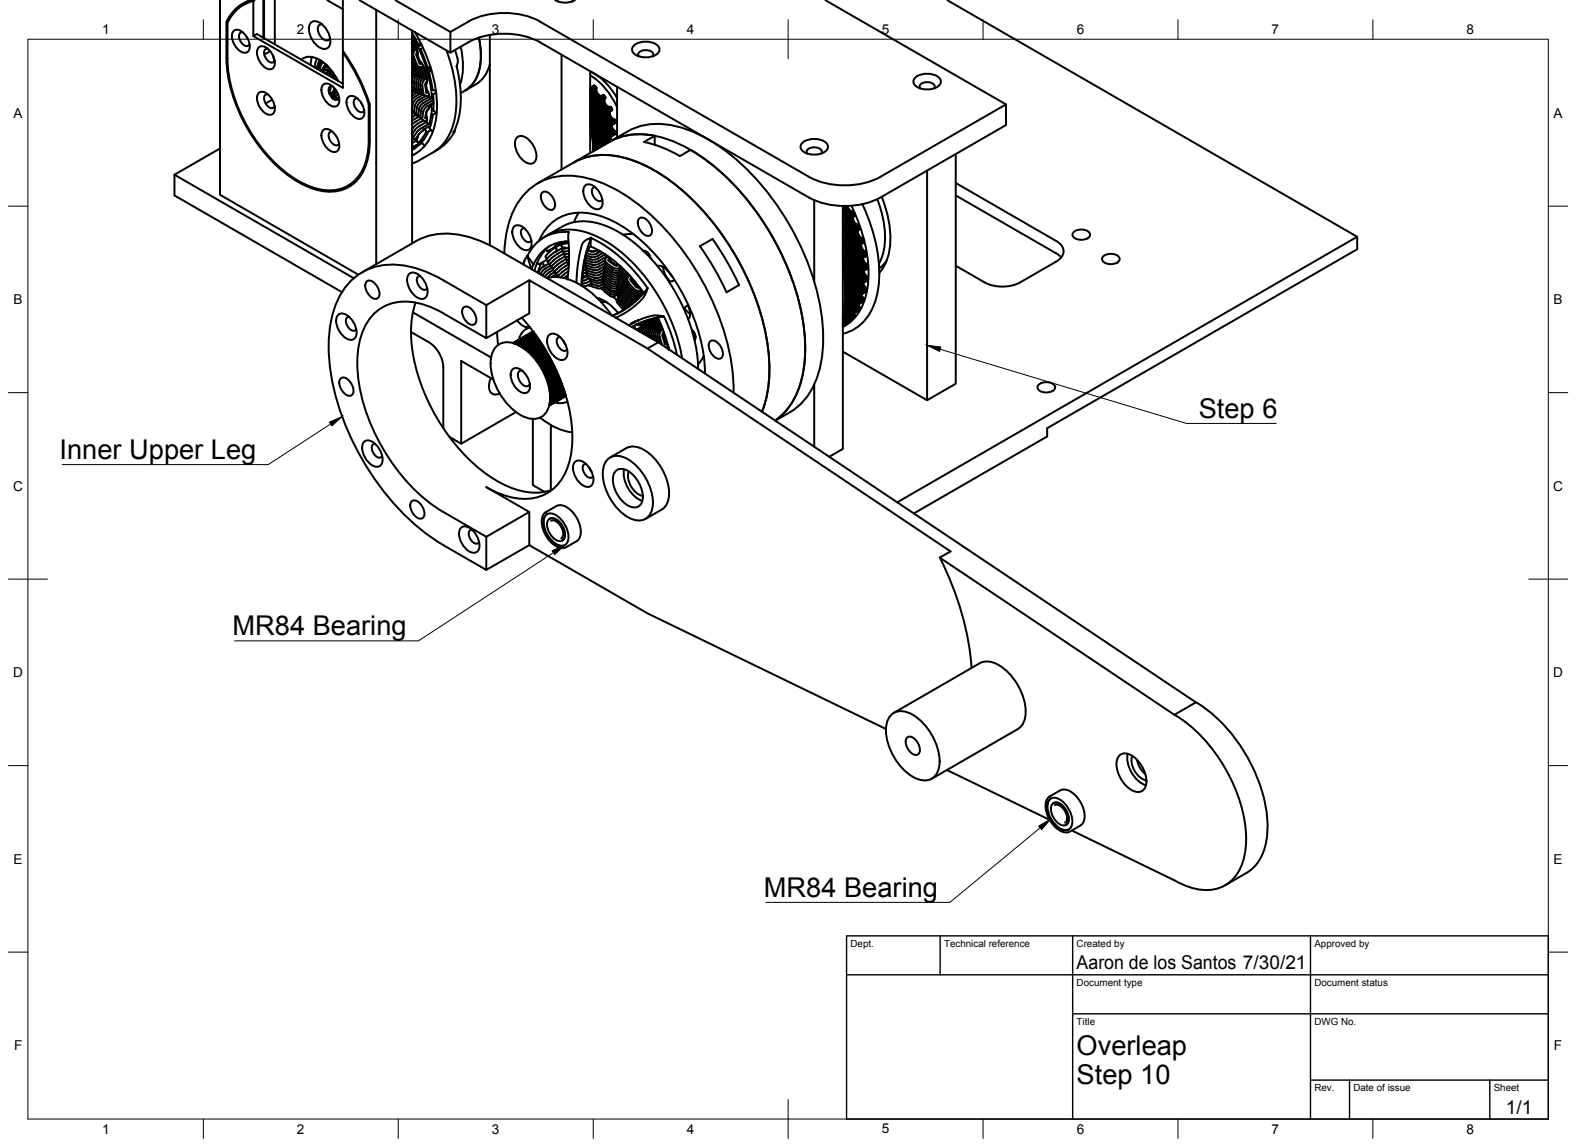
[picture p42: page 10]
Dept.; Technical reference; Created by; Approved by; Document type; Document status; Title; DWG No.; Step 10; Overleap; MR84 Bearing; Step 6

Inner Upper Leg

Aaron de los Santos

A

A

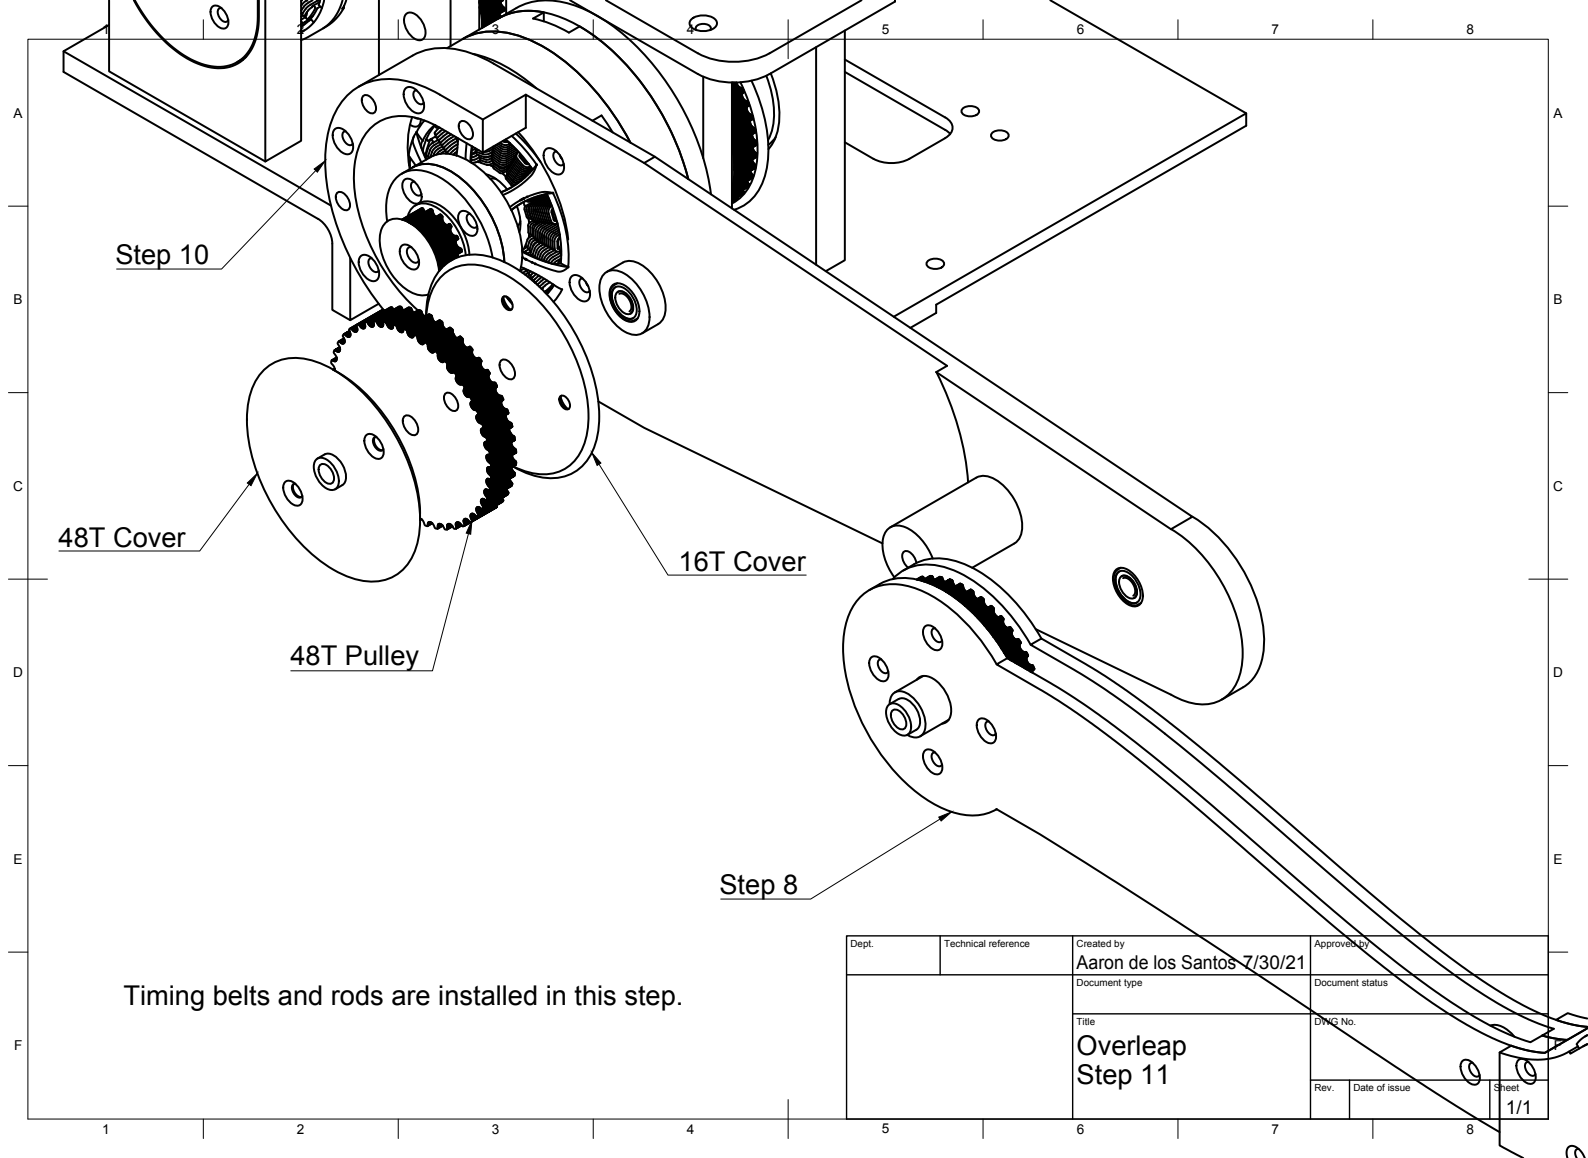
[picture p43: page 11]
Dept.; Technical reference; Created by; Approved by; Document type; Document status; Title; DWG No.; Step 11; Overleap; Step 8; Step 10; 48T Cover; 48T Pulley; 16T Cover

Aaron de los Santos

Timing belts and rods are installed in this step.

A

A

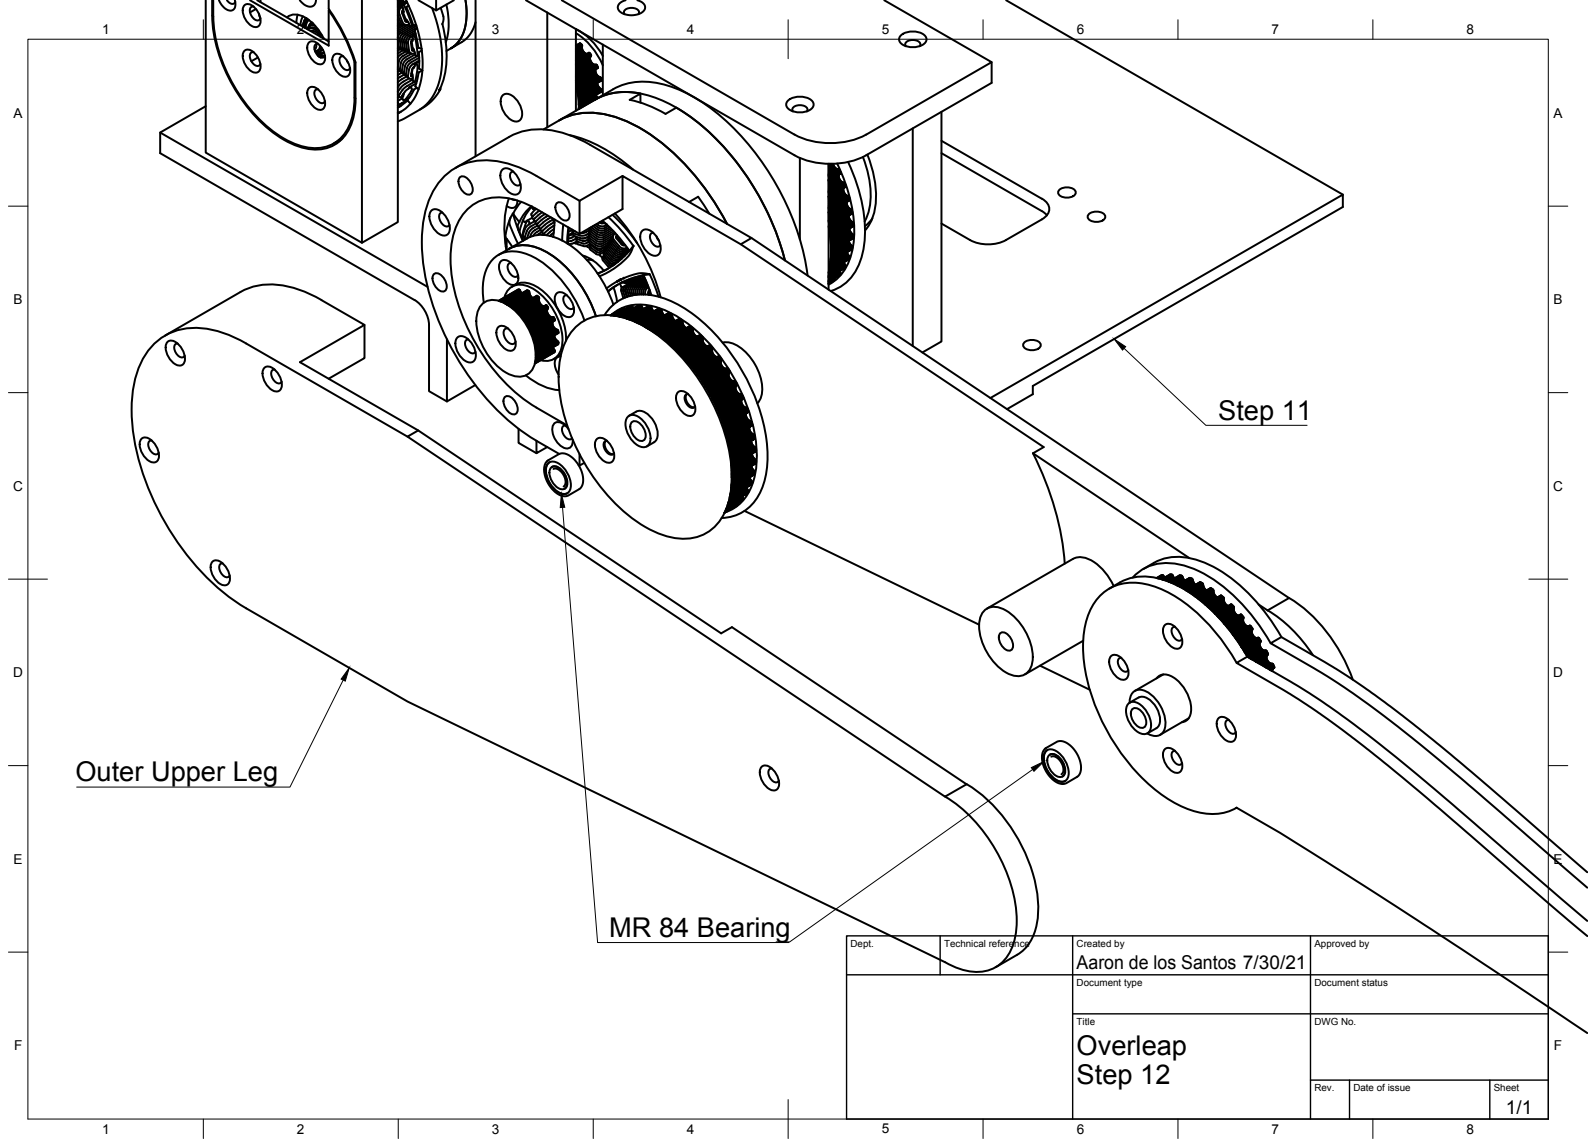
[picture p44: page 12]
Dept.; Technical reference; Created by; Approved by; Document type; Document status; Title; DWG No.; Step 12; Overleap; Step 11; MR 84 Bearing

Outer Upper Leg

Aaron de los Santos

A

A

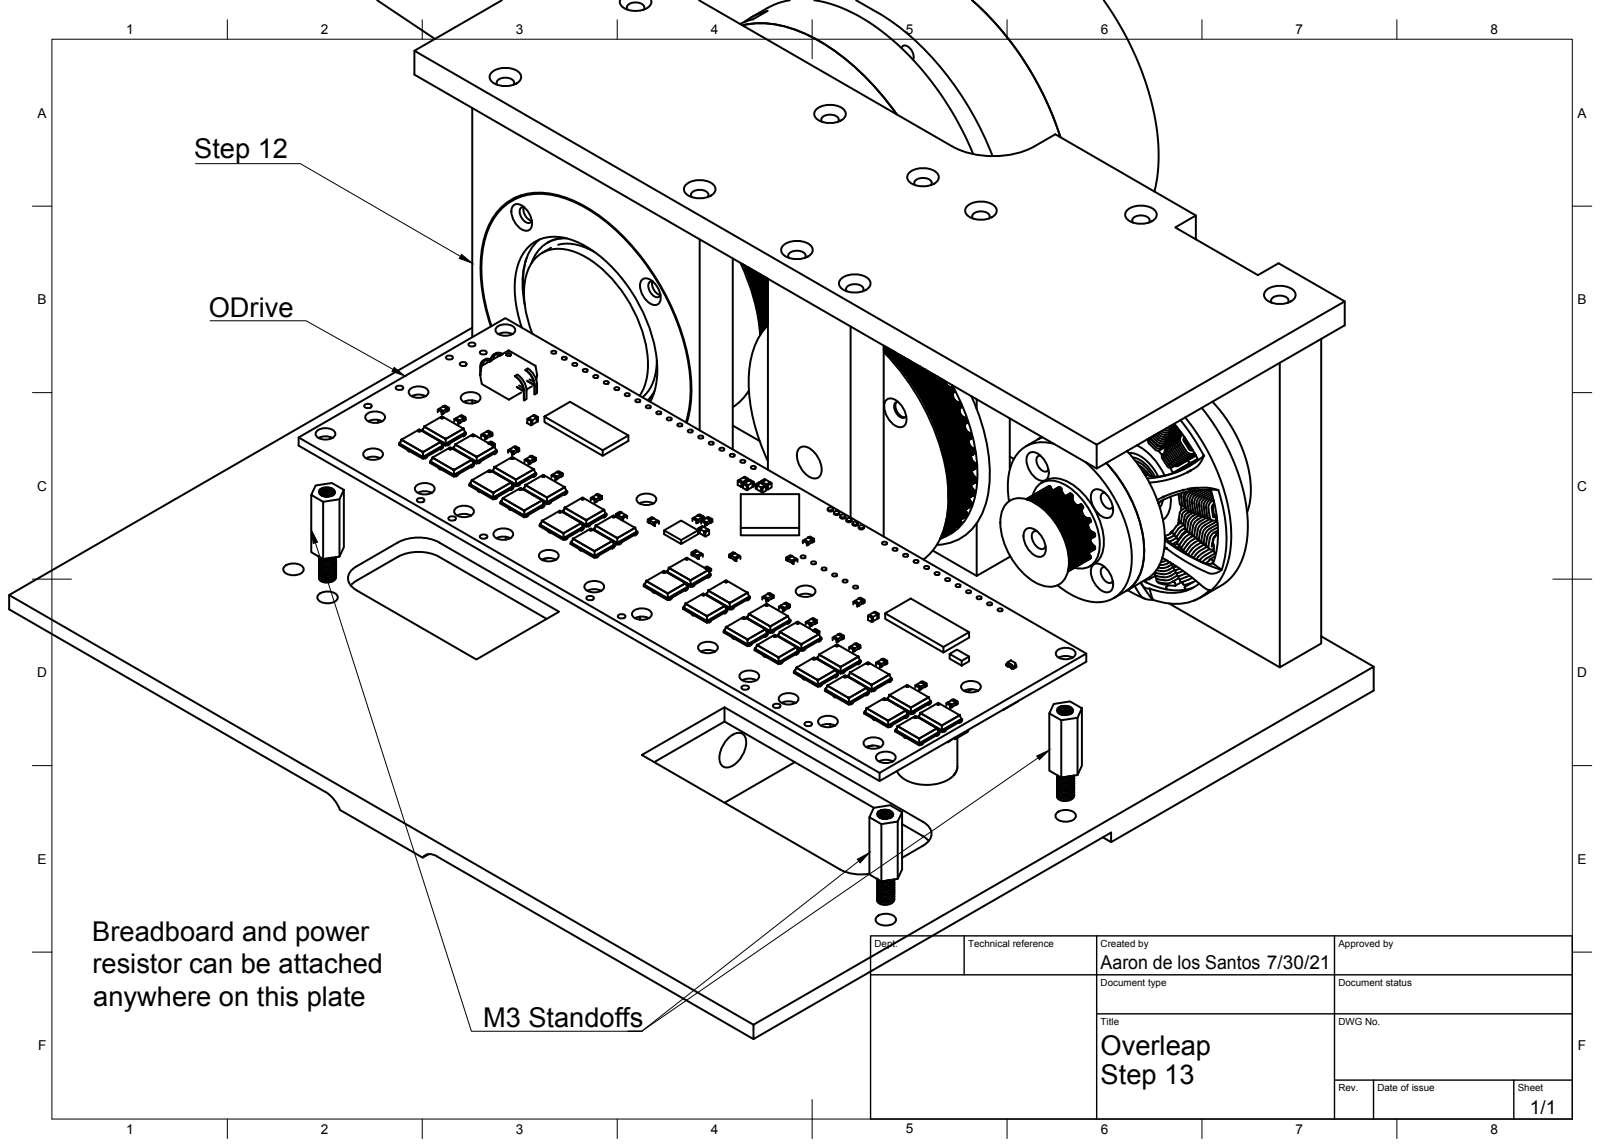
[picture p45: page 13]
Dept.; Technical reference; Created by; Approved by; Document type; Document status; Title; DWG No.; Step 13; Overleap; Step 12; ODrive; M3 Standoffs

Breadboard and power
resistor can be attached
anywhere on this plate

Aaron de los Santos

A

A

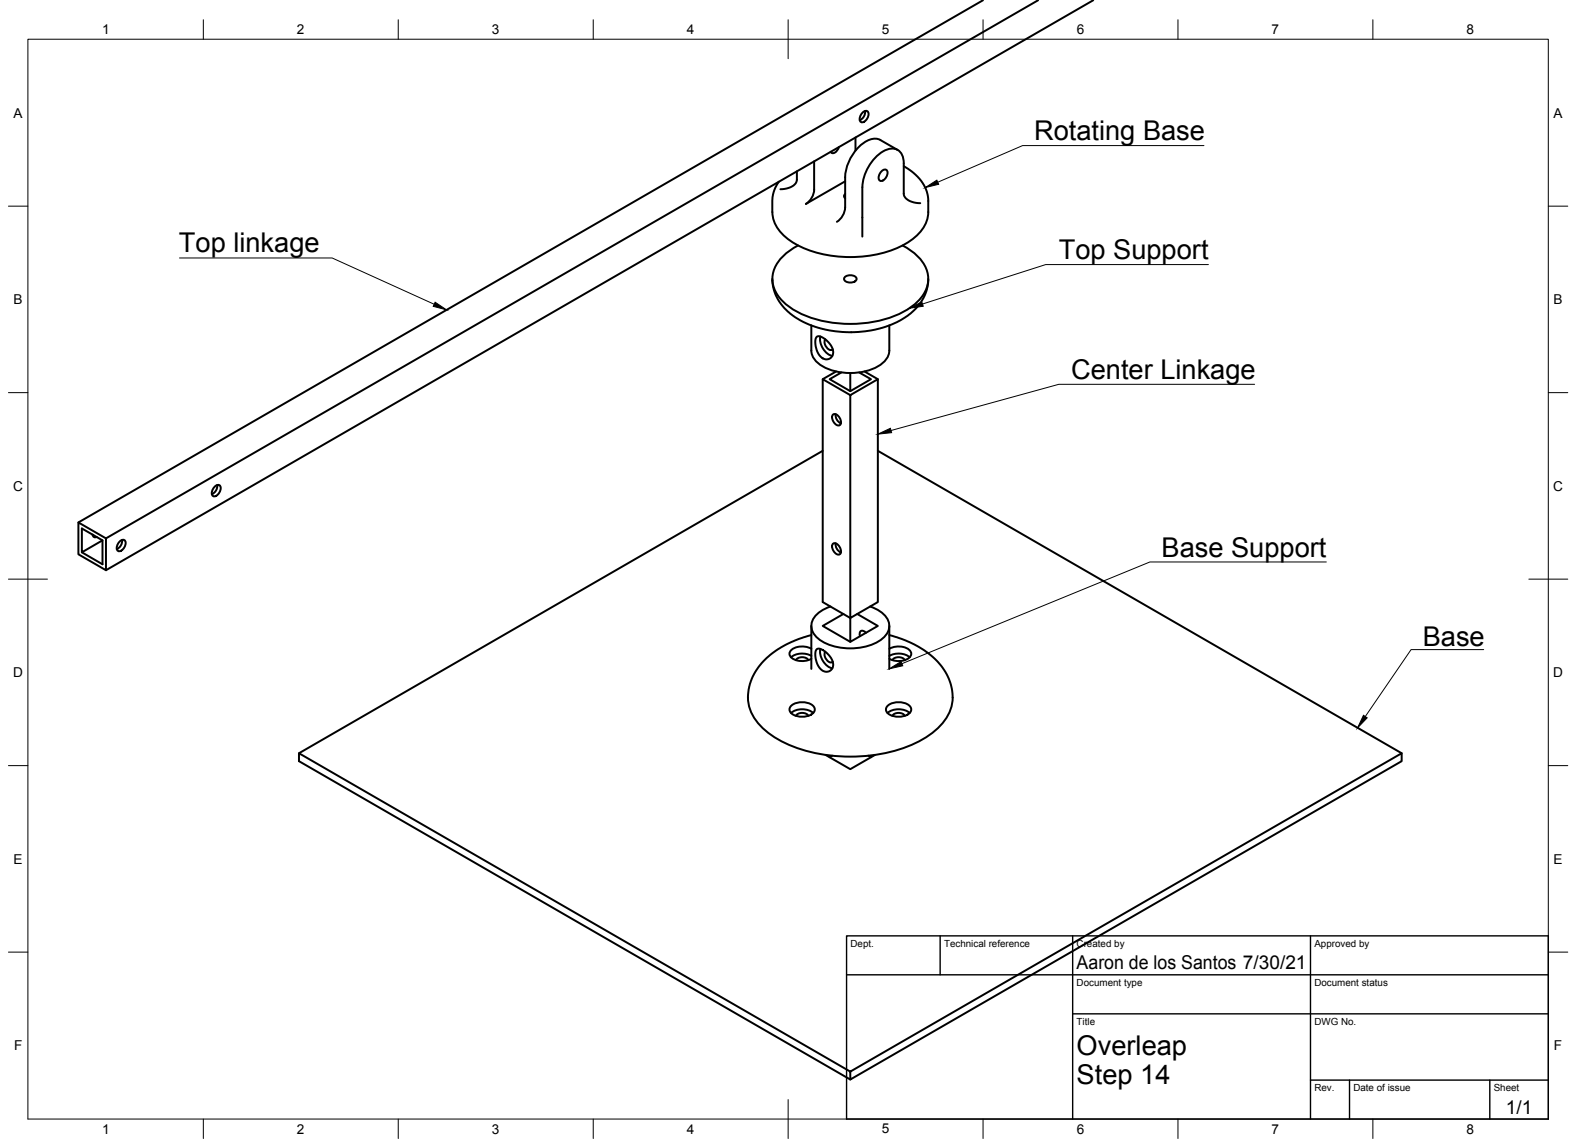
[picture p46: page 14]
Dept.; Technical reference; Created by; Approved by; Document type; Document status; Title; DWG No.; Step 14; Overleap; Top linkage; Center Linkage; Base Support; Top Support; Rotating Base; Base

Aaron de los Santos

A

A

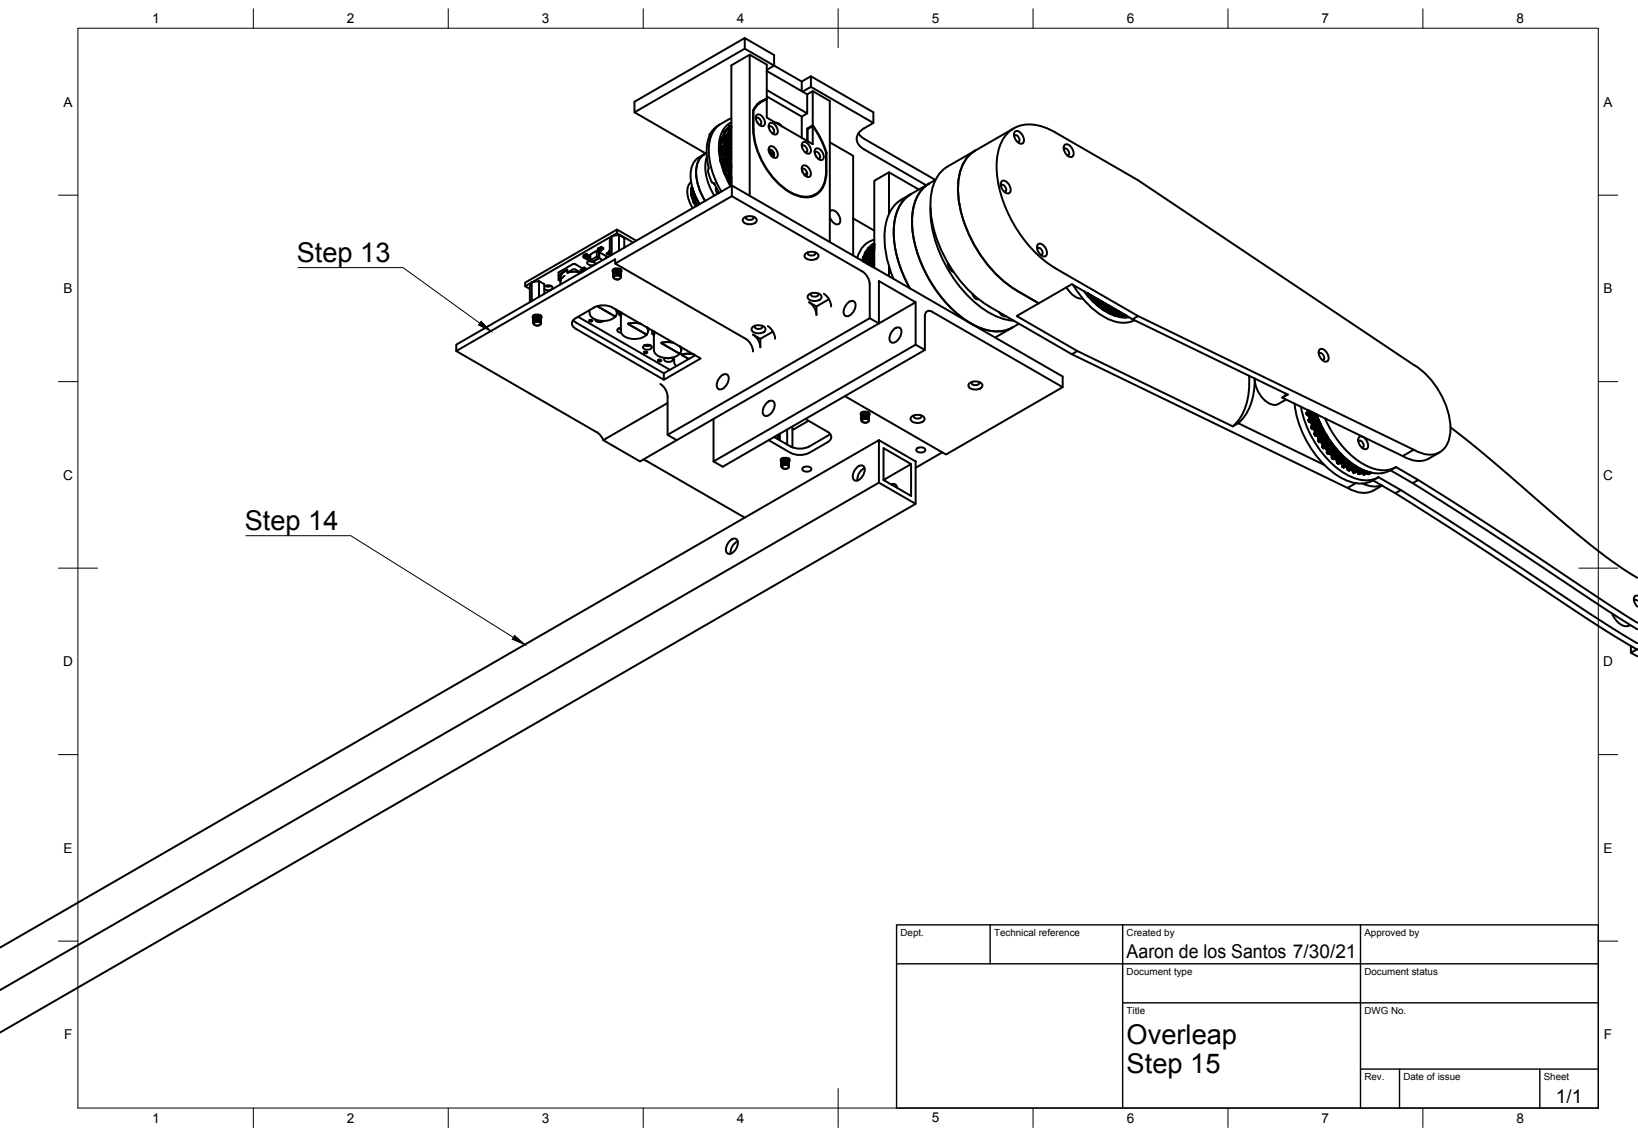
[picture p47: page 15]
Dept.; Technical reference; Created by; Approved by; Document type; Document status; Title; DWG No.; Step 15; Overleap; Step 14; Step 13

Aaron de los Santos

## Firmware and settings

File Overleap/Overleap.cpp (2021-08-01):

#include "Overleap.h"

Overleap::Overleap(float length_0, float length_1, Stream& odrive_serial, Stream& arduino_serial, ODriveArduino& odrive) : odrive_serial_(odrive_serial), arduino_serial_(arduino_serial), odrive_(odrive) {
    length_0_ = length_0;
    length_1_ = length_1;

    // initialize to 0
    theta0_zero_position_ = 0;
    theta1_zero_position_ = 0;

    // initialize to false
    calibrated_angles_ = false;

    // initialize to ground
    current_phase_ = TOUCHDOWN_PHASE;

    // set force duration
    PrepareForceProfile();
}

void Overleap::SearchEncoderIndex() {
    int requested_state = AXIS_STATE_ENCODER_INDEX_SEARCH;
    for (int motor = 0; motor<=1; motor++) {
        arduino_serial_.print("Searching for index on motor ");
        arduino_serial_.println(motor);
        if(!odrive_.run_state(motor, requested_state, true, 5.0f)) {
            arduino_serial_.println("Unsuccessful. Ending.");
            break;
        }
        arduino_serial_.print("Sucessfully found index for motor ");
        arduino_serial_.println(motor);
        arduino_serial_.println(odrive_.readFloat());
        arduino_serial_.println(odrive_.readFloat());
    }
}

MotorTorquePair Overleap::CalculateTorques(float f_x, float f_y) {
    MotorTorquePair torque_pair = {0.0f,0.0f};
    
    // Ensure positive and negative angle direction is correct
    // Gear ratio is 9:1

    // This is in radians
    float axis0_position, axis1_position;

    axis0_position = odrive_.GetPosition(0);
    float theta_0 = ((axis0_position-theta0_zero_position_)/9.0f) * 2.0f * PI;

    axis1_position = odrive_.GetPosition(1);
    float theta_1 = ((theta1_zero_position_-axis1_position)/9.0f) * 2.0f * PI;

    // use Jacobian
    // In this calculation, positive fx is to the right, negative fx is to the left
    // positive fy is downwards, negative fy is upwards
    // May be changed to sinf if desired
    // torque 0
    torque_pair.motor_0 = ( (length_0_ * sin(theta_0) + (length_1_ * sin(theta_0+theta_1))) * f_x) + ( ((-length_0_ * cos(theta_0)) + (-length_1_ * cos(theta_0+theta_1))) * f_y);
    // torque 1
    torque_pair.motor_1 = (length_1_ * sin(theta_0+theta_1) * f_x) + (-length_1_ * cos(theta_0+theta_1) * f_y);

    // consider gear ratio
    torque_pair.motor_0 /= 9.0f;
    torque_pair.motor_1 /= 9.0f;

    return torque_pair;
}

bool Overleap::LowBatteryVoltage() {
  odrive_serial_.print("r vbus_voltage\n");
  float voltage = odrive_.readFloat();
  arduino_serial_.print("Current battery voltage is: ");
  arduino_serial_.println(voltage);
  return (voltage<12); 
}


bool Overleap::WithinSafeAngles() {
  // This is in degrees
  // This depends on motor orientation
  float theta_0 = ((odrive_.GetPosition(0)-theta0_zero_position_)/9.0f) * 360.0f;
  float theta_1 = ((theta1_zero_position_-odrive_.GetPosition(1))/9.0f) * 360.0f;

  if (theta_0 < -10 || theta_0 > 75) return false;
  if (theta_1 < 0 || theta_1 > 135) return false;

  return true;    
}

bool Overleap::SafeTorqueDirection(MotorTorquePair torque_pair) {
  // for axis 0, positive torque and velocity clockwise
  // for axis 1, positive torque and velocity counterclockwise
  float theta_0 = ((odrive_.GetPosition(0)-theta0_zero_position_)/9.0f) * 360.0f;
  float theta_1 = ((theta1_zero_position_-odrive_.GetPosition(1))/9.0f) * 360.0f;
  
  if (theta_0 < -10 && torque_pair.motor_0 < 0) {
    // Upper leg is too far counterclockwise, so torque cannot be counterclockwise
    return false;
  }
  
  if (theta_0 > 75 && torque_pair.motor_0 > 0) {
    // Upper leg is too far clockwise, so torque cannot be clockwise 
    return false;
  }

  if (theta_1 < 0 && torque_pair.motor_1 > 0) {
    // Lower leg is too far counterclockwise, so torque cannot be counterclockwise
    return false;
  }
  
  if (theta_1 > 135 && torque_pair.motor_1 < 0) {
    // Lower leg is too far clockwise, so torque cannot be clockwise 
    return false;
  }

  return true;
}

bool Overleap::Touchdown() {
    int FSR_value = analogRead(0);
    // adjust based on sensor
    return (FSR_value > 1);
}

void Overleap::PrepareForceProfile() {
    // we will define the force duration to be 200ms, so b=1/duration=1/250=0.005
    // note force profile is in ms
    force_profile_.duration = 200.0f;
    force_profile_.b = 0.005f;

    // set all other values to zero to protect against executing random force profile inadvertently
    force_profile_.a = 0;
    force_profile_.fx_proportion = 0;
    force_profile_.max_fx_force = 0;
}

void Overleap::UpdateForceProfile(float force_impulse, float fx_max, float fx_proportion) {
    // Use constant profile by default
    // Another way is to take into consideration takeoff and touchdown times
  
    arduino_serial_.println("Updating force profile.");

    // We will define a constant force impulse in N ms
    // this is special case for 200ms force duration; found through intgerating the force profile for one duration
    force_profile_.a = force_impulse/100.0f;

    force_profile_.max_fx_force = fx_max;
    force_profile_.fx_proportion = fx_proportion;
}

void Overleap::UpdatePhase() {
    // here, "current" phase is the "last" phase, until it is updated
    // require "two" touchdowns to avoid error
    if (Touchdown() && Touchdown()) {
        /*
        if (current_phase == AERIAL_PHASE) { // this is still the last phase
            // last in air
            // for now, our force profile is constant
            // UpdateForceProfile();
        }
        */
        // set phase to touchdown
        current_phase_ = TOUCHDOWN_PHASE;
    } else {
        /*
        if (current_phase == TOUCHDOWN_PHASE) {
            // set takeoff time
            // for now, no need
        }
        */
        current_phase_ = AERIAL_PHASE;
    }
}

bool Overleap::RequestControlMode(int axis, int requested_control_mode, int timeout) {
    int timeout_counter = timeout * 10;

    odrive_serial_.print("w axis");
    odrive_serial_.print(axis);
    odrive_serial_.print(".controller.config.control_mode ");
    odrive_serial_.print(requested_control_mode);
    odrive_serial_.print("\n");

    do {
        delay(100);
        odrive_serial_.print("r axis");
        odrive_serial_.print(axis);
        odrive_serial_.print(".controller.config.control_mode");
        odrive_serial_.print("\n");
        timeout_counter--;
    } while (timeout_counter > 0 && odrive_.readInt() != requested_control_mode);

    return (timeout_counter > 0);
}
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

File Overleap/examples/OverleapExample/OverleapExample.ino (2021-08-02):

// Required headers
#include "Overleap.h"
#include <HardwareSerial.h>
#include <SoftwareSerial.h>
#include <ODriveArduino.h>
#include <ODriveEnums.h>

HardwareSerial& odrive_serial = Serial1;
ODriveArduino odrive(odrive_serial);

// Declare overleap leg
Overleap leg(0.19f, 0.22f, odrive_serial, Serial, odrive);

void setup() {
  // 9600 baud rate
  delay(1000);
  Serial.begin(9600);
  while (!Serial); // wait for Arduino Serial Monitor
  
  delay(1000);
  // ODrive uses 115200 baud
  odrive_serial.begin(115200);

  delay(1000);

  // Search for encoder index on both axis
  leg.SearchEncoderIndex();

  Serial.println("OverleapOS loaded.");
  Serial.println("c to calibrate angles");
  Serial.println("d to show current position in degrees and current velocity");
  Serial.println("j to perform a single jump");
  Serial.println("g for go perform multiple jumps in circular direction");
  Serial.println("y to check positive direction of torque");
  Serial.println("i for idle");

  // Check battery voltage
  if (leg.LowBatteryVoltage()) {
    Serial.println("Warning: Low battery voltage");
  }
}

void loop() {
  if (Serial.available()) {
    char c = Serial.read();
    Serial.print("Read ");
    Serial.println(c);

    if (c == 'c') {
      leg.CalibrateAngles();
    }

    if (c == 'd') {
        const unsigned long duration = 2000;
        unsigned long start = millis();

        while (millis() - start < duration) {
            // Print leg position, velocity, and whether position is within safe limits
            leg.PrintLegPosVel();
        }

    }

    if (c == 'j') {
      Serial.println("Executing a single jump.");

      // set phase to ground
      leg.SetCurrentPhase(TOUCHDOWN_PHASE);

      if (!leg.EnterTorqueControl()) {
        Serial.println("Aborting.");
        return;
      }

      // Set the impulse provided by the force profile, the maximum fx force and proportion of fy applied as fx
      // This is needed to be called before ExecuteForceProfile
      // Since a single jump is desired to go straight up, fx_max is set to 0
      leg.UpdateForceProfile(2500.0f, 0, 0.4f);
      
      // prepare to jump stance
      leg.HoldPosition(25.0f, 110.0f, false, 3000);

      // execute single force profile
      leg.ExecuteForceProfile();
      
      // tuck leg in position to avoid ground and be ready for next jump
      // ends if either time runs out or if touchdown occurs
      // next force profile can execute if expected to touchdown soon, even without currently touching ground
      leg.HoldPosition(25.0f, 110.0f, true, 800);

      // and we go to raised stance with ample time to secure leg before powering down
      leg.HoldPosition(45.0f, 90.0f, false, 3000);

      delay(100);
        
      leg.RequestIdleState();
    }

    if (c == 'g') {
      Serial.println("Go for executing multiple jumps.");

      // Set starting phase to ground
      leg.SetCurrentPhase(TOUCHDOWN_PHASE);

      if (!leg.EnterTorqueControl()) {
        Serial.println("Aborting.");
        return;
      }

      // do the initial jump
      
      // update force profile
      leg.UpdateForceProfile(2200.0f, 10.0f, 0.4f);
      
      // prepare to jump stance
      leg.HoldPosition(25.0f, 110.0f, false, 3000);

      // execute single force profile
      leg.ExecuteForceProfile();

      // tuck leg in position to avoid ground and be ready for next jump
      // ends if either time runs out or if touchdown occurs
      // next force profile can execute if expected to touchdown soon, even without currently touching ground
      leg.HoldPosition(25.0f, 110.0f, true, 800);

      // after the initial jump, we can now do multiple consecutive jumps
      // start by updating the force profile to account for downward momentum
      // this value is empirical, but can be changed to account for takeoff and touchdown times
      leg.UpdateForceProfile(2600.0f, 10.0f, 0.4f);
      
      for (int jump=1; jump<10; jump++) {
        // execute single force profile
        leg.ExecuteForceProfile();
        // ready for landing and end at touchdown or 800ms
        leg.HoldPosition(25.0f, 110.0f, true, 800);
      }
      
      // Put into raised stance to secure leg before powering down
      leg.HoldPosition(45.0f, 90.0f, false, 4000);

      delay(100);
        
      leg.RequestIdleState();
    }

    if (c == 'y') {
      Serial.println("Torque direction check.");

      if (!leg.EnterTorqueControl()) {
        Serial.println("Aborting.");
        return;
      }

      for (int axis=0; axis<=1; axis++) {
        Serial.print("Type 'r' when ready for axis "); Serial.print(axis); Serial.print(": ");
        char read_char = 'a';
        while (read_char != 'r') {
            while (!Serial.available()) {
                delay(100);
            }
            read_char = Serial.read();
        }

        const unsigned long duration = 1000;
        unsigned long start = millis();
        float torque = 0.02;

        // delay by a bit
        delay(200);

        while (millis() - start < duration) {
          odrive_serial.print("c "); 
          odrive_serial.print(axis); 
          odrive_serial.print(" ");
          odrive_serial.print(torque,3); 
          odrive_serial.print("\n");
        }

        // command zero torque
        odrive_serial.print("c "); 
        odrive_serial.print(axis);
        odrive_serial.print(" 0"); 
        odrive_serial.print("\n");
      }

      Serial.println("Ending torque direction check.");

      delay(100);
        
      leg.RequestIdleState();
    }

    if (c == 'i') {
      leg.RequestIdleState();
    }
  }
}

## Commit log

2021-08-01 Added assembly and circuit drawings
2021-08-01 Added parts list
    [16T Cover.stl, 16T Pulley.stl, 6706 Bearing Housing.stl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]
2021-08-01 Added assembly instructions
    Changed image filenames to remove spaces
2021-08-01 Added ODrive set-up guide
2021-08-01 Added Overleap Arduino library
2021-08-01 Added arduino library guide
2021-08-01 Fixed circuit drawing link
2021-08-02 Fixed end position of jump
    [OverleapExample.ino]
